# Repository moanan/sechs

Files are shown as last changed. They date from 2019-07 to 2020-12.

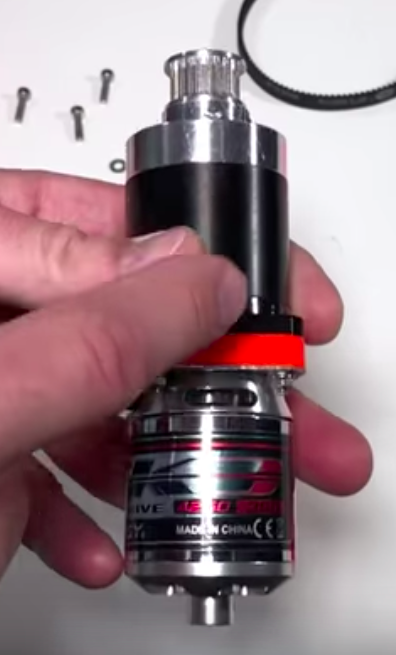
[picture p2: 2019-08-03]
2-hardware/motor/Screenshot 2019-07-31 at 23.09.07.png

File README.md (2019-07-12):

# sechs

直接在main.py中定义robot的dh参数，工具，负载，角加速度。

调用robot.frame得到各个轴的空间方位

调用robot.frame.origin得到各个轴的空间位置

调用robot.torque(tool, payload, acceleration)得到各个轴所需的转矩

调用robot.visualization(tool, payload, acceleration)可视化

torque的计算方法：

  第i个轴的torque为：abs(往后各轴以及末端负载对第i轴z_axis的力矩和) + 往后各轴以及末端负载的总惯性矩 * 预设的角加速度

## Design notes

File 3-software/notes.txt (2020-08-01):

DH parameters to urdf file: https://adohaha.github.io/DH2URDF/

```
ssh sechs@192.168.179.121
```
password: ubuntu
vncserver password: 123456

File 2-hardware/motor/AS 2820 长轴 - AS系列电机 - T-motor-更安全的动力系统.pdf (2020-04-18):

18/04/2020 | AS 2820 长轴 - AS系列电机 - T-motor-更安全的动⼒系统

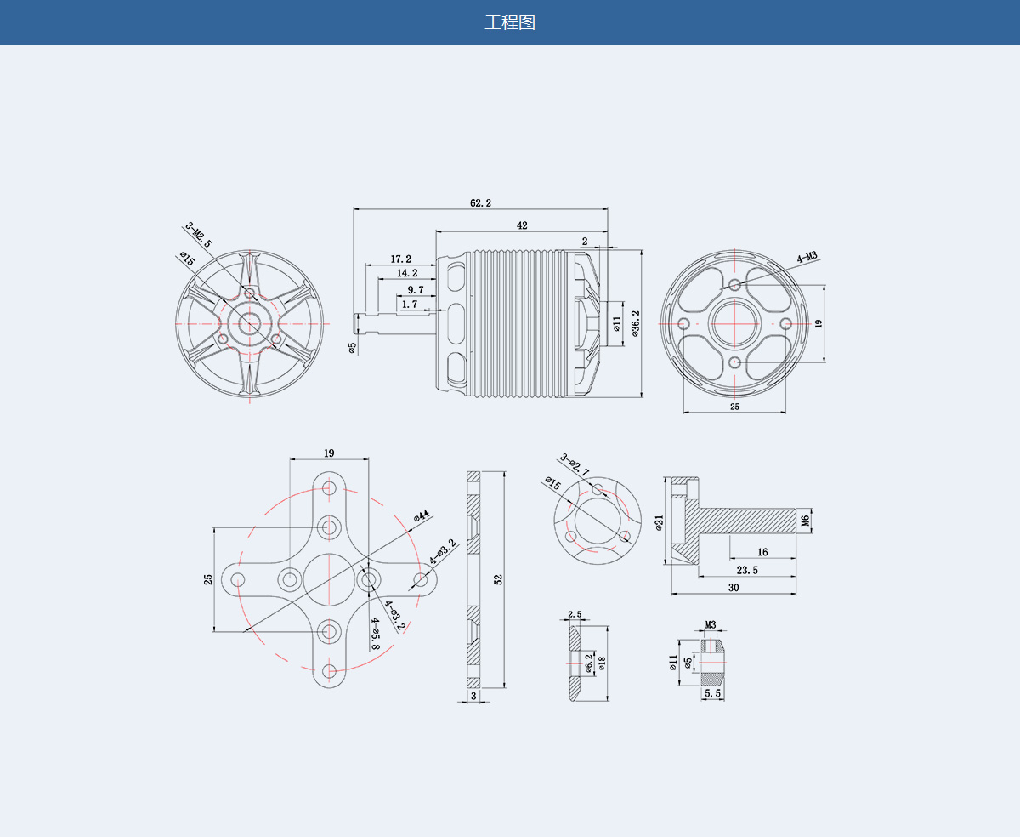
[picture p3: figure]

uav-cn.tmotor.com/html/uav/html/2019/as_1129/312.html | 1/6
AS 2820 ⻓轴 | 详情 | 参数 | ⽴即购买 (http://store-cn.tmotor.com/goods.php?id=921)

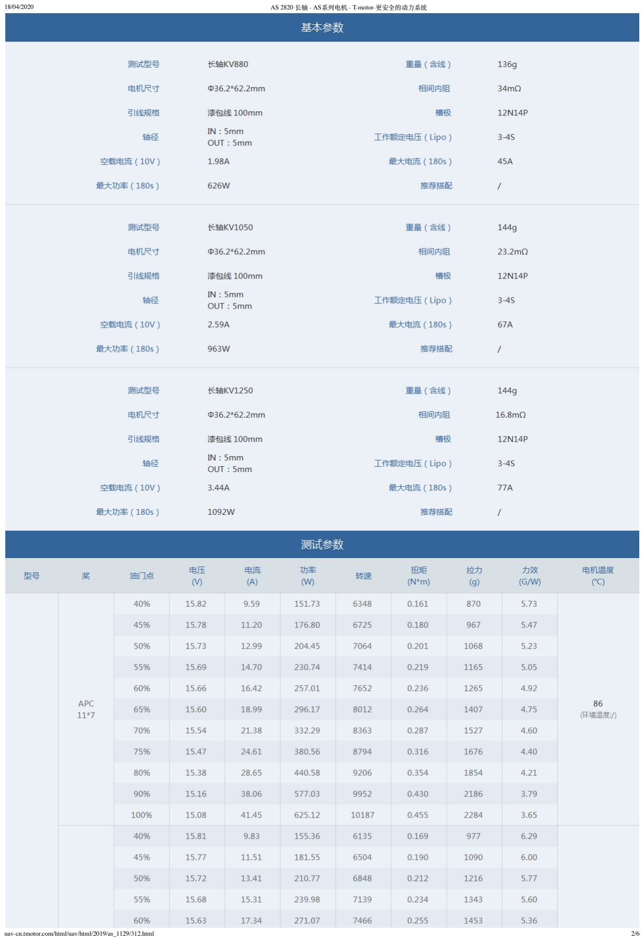
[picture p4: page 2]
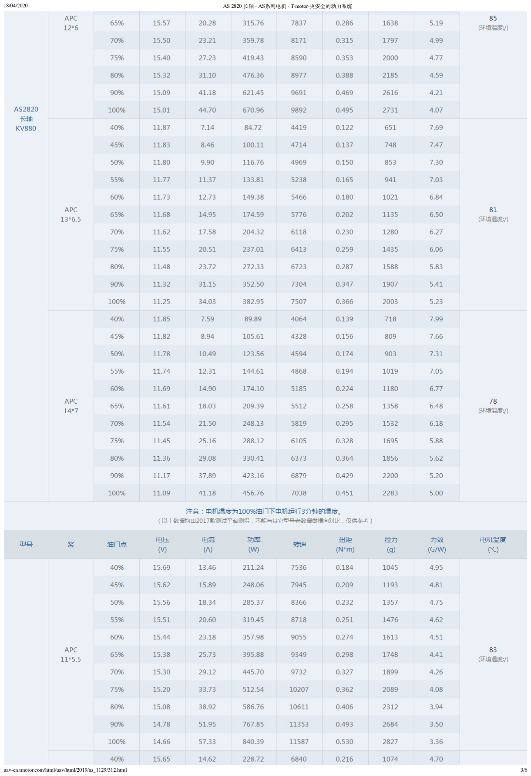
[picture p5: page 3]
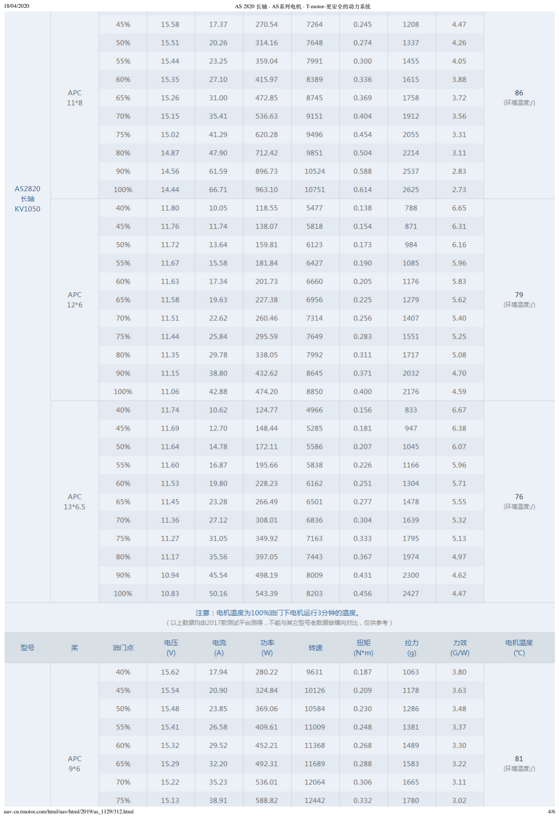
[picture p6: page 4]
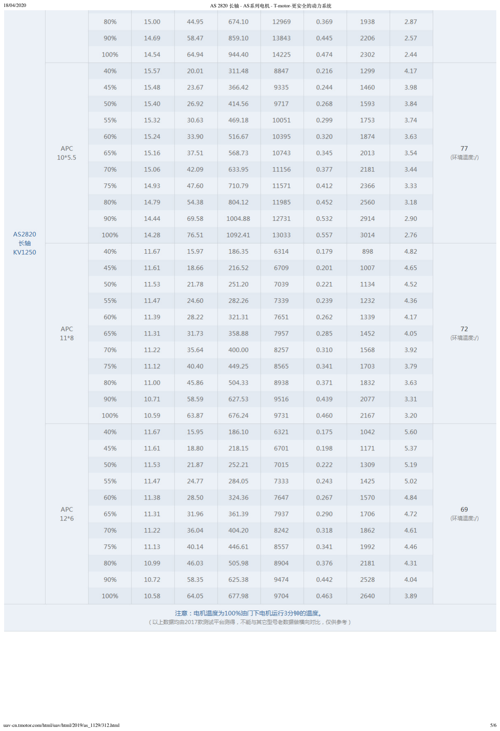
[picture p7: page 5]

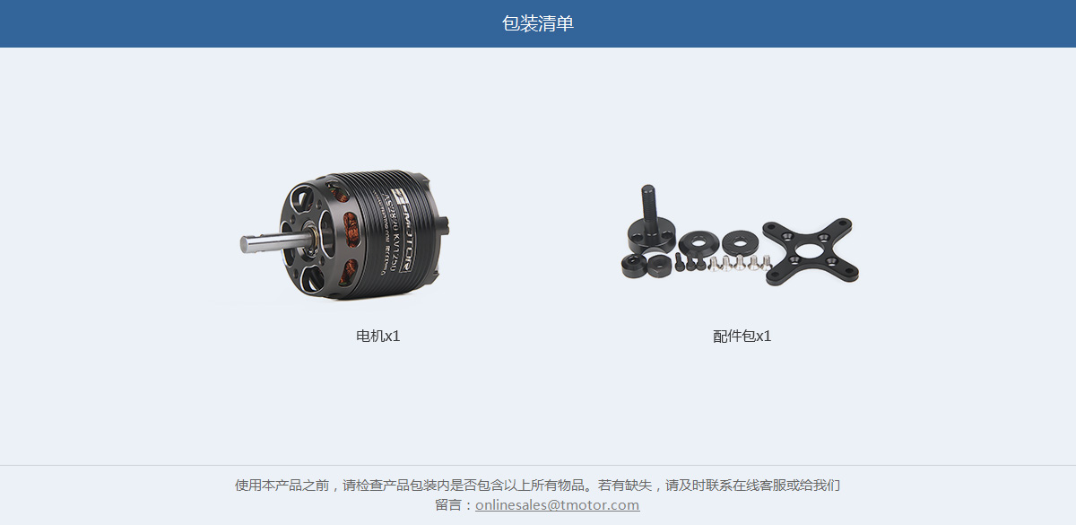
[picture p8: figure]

## English (http://uav-en.tmotor.com/)

关于我们 | | 联系我们 | | 加⼊我们 | | 精彩动态 | | 授权经销商 (https://www.facebook.com/rctigermotor)

## Copyright © 2003-2018 T-motor, All rights reserved. 赣ICP备17011325号-1

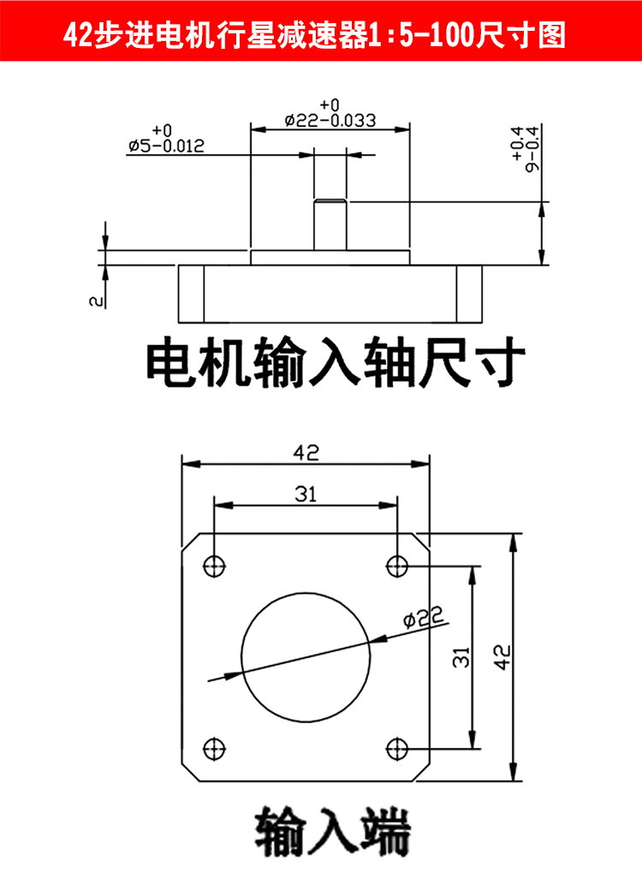
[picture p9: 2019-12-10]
2-hardware/gearbox/d1.jpg

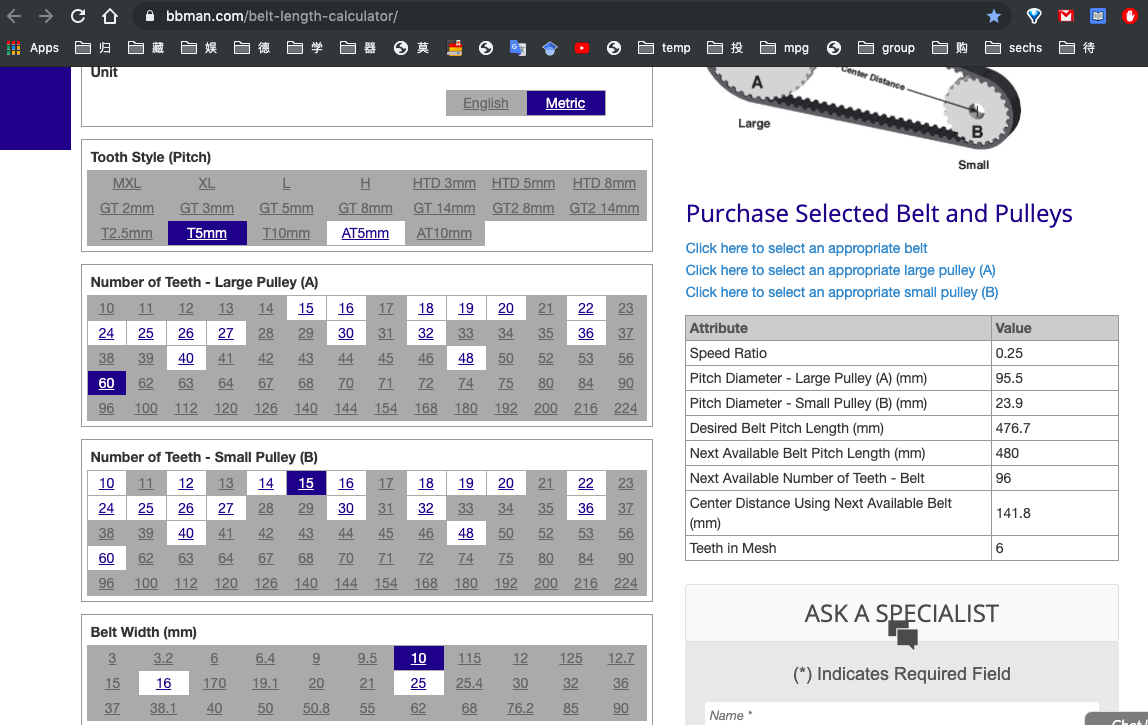
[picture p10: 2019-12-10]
2-hardware/timming belt/Screenshot 2019-11-13 at 22.11.02.png

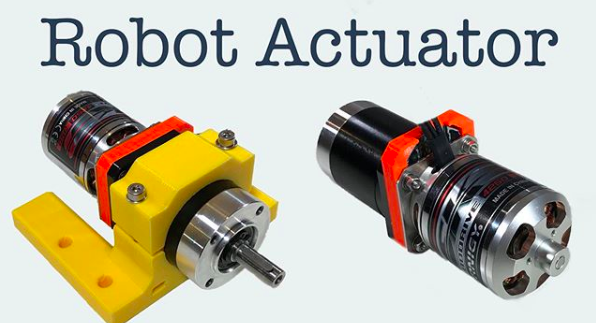
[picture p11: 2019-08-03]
2-hardware/motor/Screenshot 2019-07-31 at 22.52.01.png

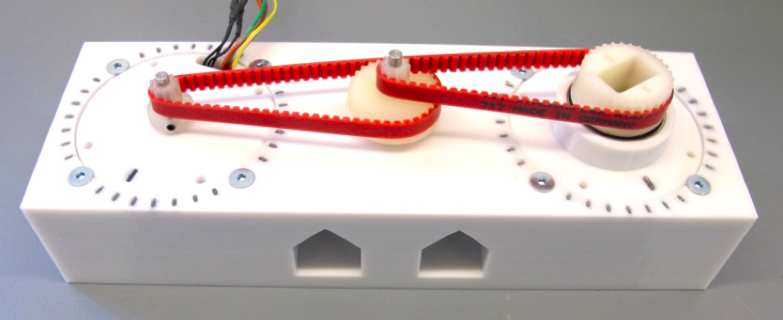
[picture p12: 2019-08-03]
2-hardware/motor/Screenshot 2019-07-21 at 15.00.27.png

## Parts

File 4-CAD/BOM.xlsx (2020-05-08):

Item | Part Number | Thumbnail | BOM Structure | Unit QTY | QTY | Stock Number | Description | REV
1 | 101-bottom | (NonDisplayable) | Normal | 1 | 1
2 | Synchronous Belt | *Varies* | Normal | 1 | 2
3 | Synchronous Pulley1 | *Varies* | Normal | 1 | 2
4 | Synchronous Pulley2 | *Varies* | Normal | 1 | 2
6 | AS5047 | (NonDisplayable) | Normal | 1 | 3
7 | magnet-6x2.5 | (NonDisplayable) | Normal | 1 | 3
8 | J1-sketch | *Varies* | Normal | 1 | 2
9 | X6215S | (NonDisplayable) | Normal | 1 | 1
10 | 104-motor-case-new | (NonDisplayable) | Normal | 1 | 1
11 | 201- | *Varies* | Normal | 1 | 3
19 | 901-4250 house | (NonDisplayable) | Normal | 1 | 2
20 | 911-42-reducer-long | (NonDisplayable) | Normal | 1 | 2
21 | Lower_Can | (NonDisplayable) | Normal | 1 | 2
22 | Shaft | (NonDisplayable) | Normal | 1 | 2
23 | Lower_Cap | (NonDisplayable) | Normal | 1 | 2
24 | Power Cables | (NonDisplayable) | Normal | 1 | 2
25 | 6mm Bearing | (NonDisplayable) | Normal | 1 | 2
26 | 5 to 6 mm bushing | (NonDisplayable) | Normal | 1 | 2
27 | Stator_Coils | (NonDisplayable) | Normal | 1 | 24
28 | Stator_Steel_Laminations | (NonDisplayable) | Normal | 1 | 2
29 | 98541A113_BLACK-FINISH STEEL EXTERNAL RETAINING RING_step | (NonDisplayable) | Normal | 1 | 2
30 | 91290A111_BLACK-OXIDE CLASS 12.9 SOCKET HEAD CAP SCREW_step | (NonDisplayable) | Normal | 1 | 8
31 | SK3 350KV Upper Assembly_MODEL | (NonDisplayable) | Normal | 1 | 2
32 | 902-4250 magnet hold | (NonDisplayable) | Normal | 1 | 2
33 | 903-4250 back | (NonDisplayable) | Normal | 1 | 2
37 | 203-link left | *Varies* | Normal | 1 | 2
42 | J4-dummy | (NonDisplayable) | Normal | 1 | 1
5 | 61814-2RS1 | (NonDisplayable) | Purchased | 1 | 2 |  | BB1_001_101-Deep groove ball bearings
18 | 61807-2RS1 | (NonDisplayable) | Purchased | 1 | 4 |  | BB1_001_101-Deep groove ball bearings
38 | W 638/3-2Z | (NonDisplayable) | Purchased | 1 | 4 |  | BB1_001_101-Deep groove ball bearings
41 | W 61705-2RZ | (NonDisplayable) | Purchased | 1 | 1 |  | BB1_001_101-Deep groove ball bearings
14 | ISO 4032 - M2 | (NonDisplayable) | Purchased | 1 | 12 |  | Hex Nut. Product grades A and B
44 | ISO 4032 - M3 | (NonDisplayable) | Purchased | 1 | 2 |  | Hex Nut. Product grades A and B
12 | ISO 10642 - M3 x 20 | (NonDisplayable) | Purchased | 1 | 4 |  | Hexagon Socket Countersunk Head Screw
15 | ISO 10642 - M4 x 16 | (NonDisplayable) | Purchased | 1 | 3 |  | Hexagon Socket Countersunk Head Screw
39 | ISO 10642 - M4 x 20 | (NonDisplayable) | Purchased | 1 | 8 |  | Hexagon Socket Countersunk Head Screw
13 | ISO 4762 - M2 x 6 | (NonDisplayable) | Purchased | 1 | 12 |  | Hexagon Socket Head Cap Screw
16 | ISO 4762 - M3 x 10 | (NonDisplayable) | Purchased | 1 | 13 |  | Hexagon Socket Head Cap Screw
17 | ISO 4762 - M4 x 20 | (NonDisplayable) | Purchased | 1 | 6 |  | Hexagon Socket Head Cap Screw
35 | ISO 4762 - M3 x 16 | (NonDisplayable) | Purchased | 1 | 8 |  | Hexagon Socket Head Cap Screw
36 | ISO 4762 - M2.5 x 12 | (NonDisplayable) | Purchased | 1 | 6 |  | Hexagon Socket Head Cap Screw
40 | ISO 4762 - M3 x 12 | (NonDisplayable) | Purchased | 1 | 12 |  | Hexagon Socket Head Cap Screw
43 | ISO 4762 - M3 x 20 | (NonDisplayable) | Purchased | 1 | 2 |  | Hexagon Socket Head Cap Screw
45 | ISO 4762 - M3 x 25 | (NonDisplayable) | Purchased | 1 | 14 |  | Hexagon Socket Head Cap Screw
34 | DIN 7991 - M3x12 | (NonDisplayable) | Purchased | 1 | 8 |  | Hexagon socket countersunk head cap screws

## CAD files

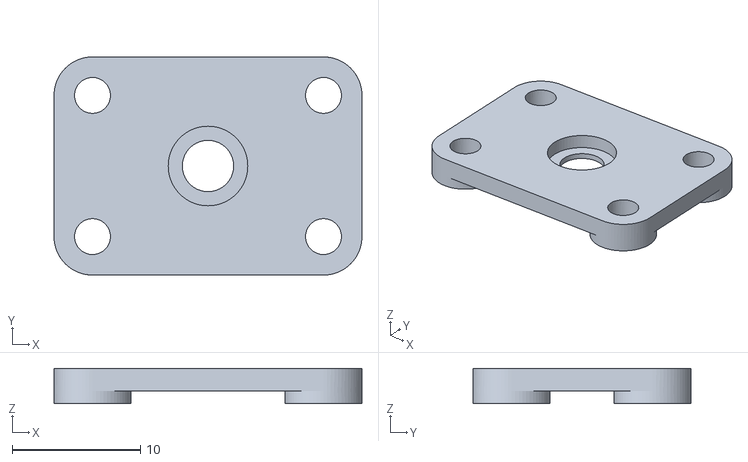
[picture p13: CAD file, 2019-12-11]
2-hardware/encoder/test_encoder.stl
24.0 x 17.0 x 2.75

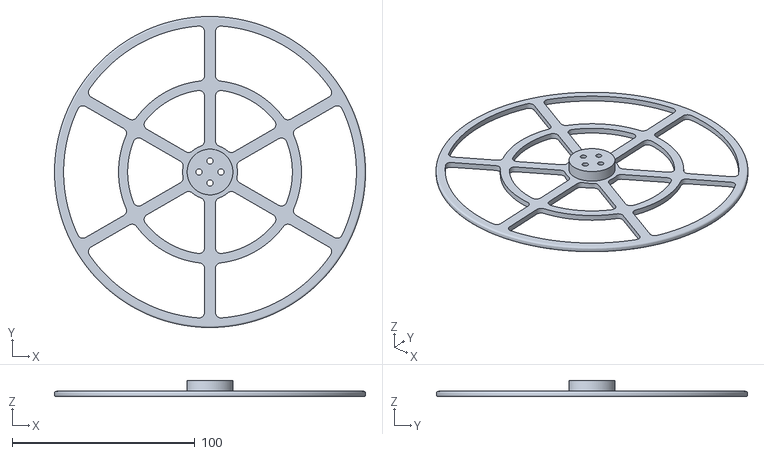
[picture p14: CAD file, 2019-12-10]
4-CAD/tester/fly.stl
170.0 x 170.0 x 9.00

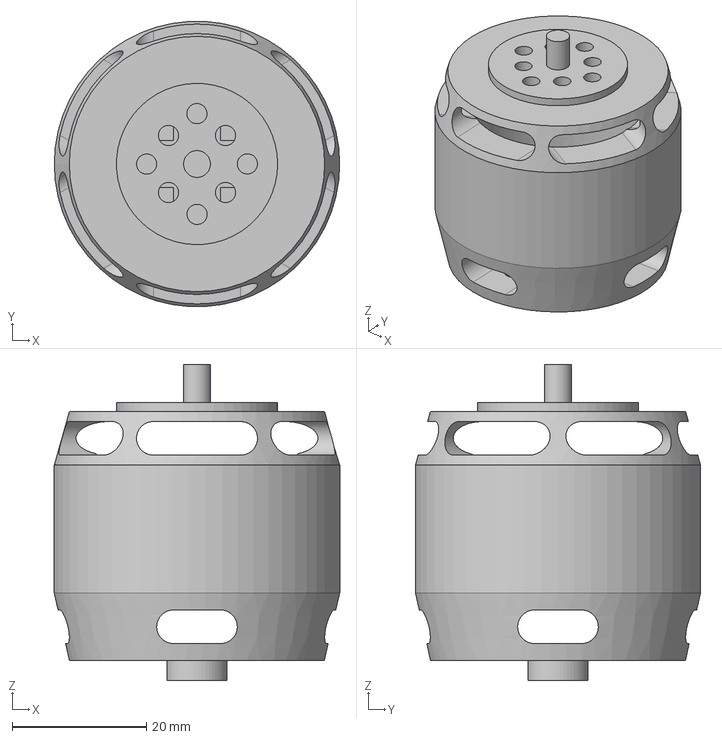
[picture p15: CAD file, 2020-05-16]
4-CAD/standardParts/AS 2820 kv880/T-MOTOR_U5 .step
42.5 x 42.4 x 47.0 mm

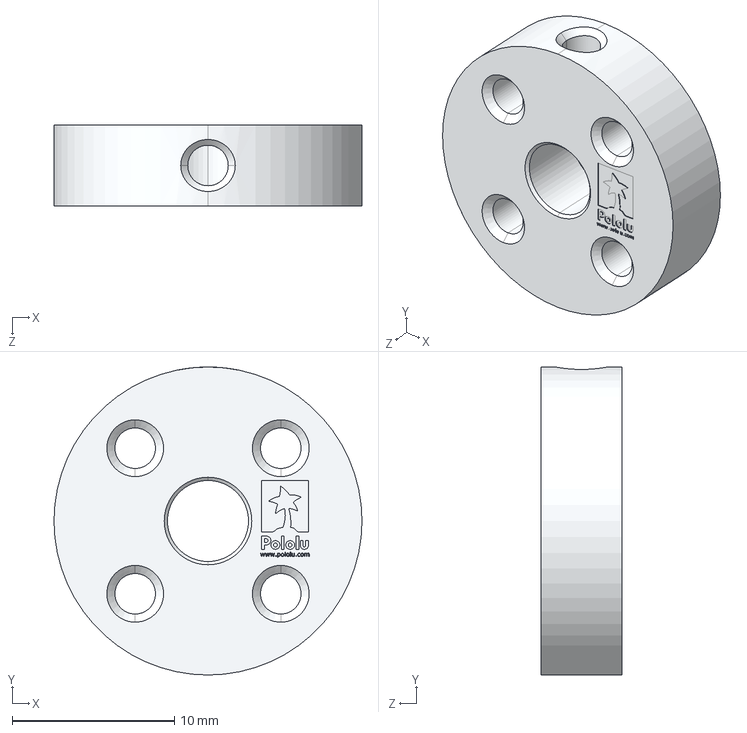
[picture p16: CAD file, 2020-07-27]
4-CAD/standardParts/Pololu mounting hub/pololu-universal-aluminum-mounting-hub-for-5mm-shaft-m3-holes.step
19.0 x 19.0 x 5.00 mm

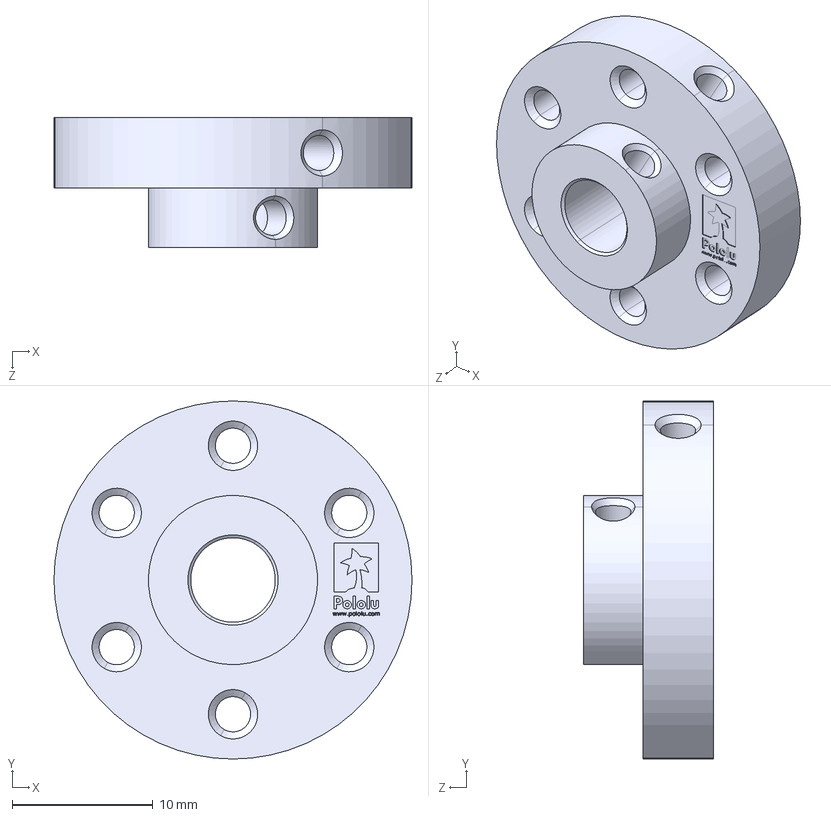
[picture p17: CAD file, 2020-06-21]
4-CAD/standardParts/Pololu mounting hub/pololu-universal-aluminum-mounting-hub-for-6mm-shaft-m3-holes.step
25.4 x 25.4 x 9.20 mm

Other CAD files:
4-CAD/standardParts/Pololu mounting hub/pololu-universal-aluminum-mounting-hub-for-8mm-shaft-m3-holes.step
2-hardware/encoder/test_encoder.3dm
4-CAD/10-J1.iam
4-CAD/10-J1_new.iam
4-CAD/102-top-motor-adapt-big-motor.ipt
4-CAD/102-top-motor.ipt
4-CAD/103-top-output.ipt
4-CAD/104-motor-case-new.ipt
4-CAD/104-motor-case.ipt
4-CAD/105-flange adapter.ipt
4-CAD/106-pulley adapter.ipt
4-CAD/111-base template.ipt
4-CAD/112-base middle.ipt
4-CAD/113-base bottom.ipt
4-CAD/114-base top.ipt
4-CAD/20-J2.iam
4-CAD/200-link template.ipt
4-CAD/201-flange-with motor.ipt
4-CAD/203-dummy.iam
4-CAD/203-link left-dummy dowm.ipt
4-CAD/203-link left-dummy up.ipt
4-CAD/203-link left.ipt
4-CAD/30-J3.iam
4-CAD/303-dummy.iam
4-CAD/303-link right-dummy down.ipt
4-CAD/303-link right-dummy up.ipt
4-CAD/303-link right.ipt
4-CAD/40-J4.iam
4-CAD/401-flange.ipt
4-CAD/402-gearbox-housing-cap.ipt
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

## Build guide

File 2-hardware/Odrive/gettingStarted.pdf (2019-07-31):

- Connect the three phases of one or both motors
- connect the brake resistor to AUX + and AUX - (resistor has no polarity)
- connect the ABI encoder (5 pins: A, B, I (or X, Z), 5V and GND)
- connect the oDrive to the computer via USB
- check that the switch on SW1 is on RUN, not on DFU (= device firmware update)
- connect the oDrive DC+ and DC- to a direct current power supply (pay attention to polarity); minimum voltage for all board versions is 12 VDC
- download and install odrivetool following these
steps: https://docs.odriverobotics.com/#downloading-and-installing-tools (offline version Getting Started _ ODrive.pdf)
- in your bash/shell, move to the directory that has odrivetool, typically in odrive/tools/, and run the tool by typing ./odrivetool; for Windows, see description on oDrive homepage(Link)
- turn on power supply with at least half of the oDrive's maximum voltage (there are 24V oDrives and 48V oDrives, higher voltages may be available online soon are available in the oDrive shop), start with low maximal current, e. g. 2A
- check if the PWR LED on your oDrive is on
- odrivetool should recognize the oDrive after some seconds
but if you want a specific oDrive to be connected, type $ ./odrivetool --serial-number <your serial number here>
set up for the motor (in this example, connected to M0, which odrivetool knows
as axis0)
- odrivetool should automatically recognize the odrive and put out a 'connected' notice
- to inspect all available parameters and variables, type odrv0 (or odrv1, depending on how many oDrives are connected)
- you can go into deeper variable levels pertaining to python objects by typing for example odrv0.config or odrv0.axis0
- first, make sure the motor will not get overloaded, so set limits (the values given here are for a T-Motor MN4006-23, 0.3A idle current, 16 A max current)
- odrv0.axis0.motor.config.current_lim = 2
- odrv0.axis0.controller.config.vel_limit = 2000 (velocity is in encoder counts / sec)
- odrv0.axis0.motor.config.calibration_current = 1
- odrv0.config.brake_resistance = 2.0
- odrv0.axis0.motor.config.pole_pairs = 12

•

# Getting started - oDrive V3.5

Wednesday, 31. July 2019 09:05

- odrv0.axis0.motor.config.pole_pairs = 12
- odrv0.axis0.motor.config.motor_type = 0 (for high current motors; for gimbal motors set motor_type = 1)
- odrv0.axis0.encoder.config.cpr = 8192 (CPR = 4xPPR, PPR being the pulses per rotation for one channel. You have to multiply by 4, since oDrive is counting both rising and falling edges for both A and B channel)
- odrv0.save_configuration() (keep this command in mind since for many errors, this command followed by odrv0.reboot() helps)
- odrv0.reboot()
now do the calibration, save and reboot again:
odrv0.axis0.requested_state = AXIS_STATE_FULL_CALIBRATION_SEQUENCE

○

•

for now, control should work; type
- odrv0.axis0.requested_state = AXIS_STATE_CLOSED_LOOP_CONTROL ← this automatically sets position control
- if calibration fails in the first place and the coils are not powered,
set odrv0.axis0.controller.config.vel_limit_tolerance = 0.0
- please not that this setting makes the controller IGNORE any velocity overshoot!

•

- tune the controller via its parameters, which you can all check by typing
- odrv0.axis0.controller.config
- you can change control mode in odrvX.axisX.controller.config.control_mode (for control modes see below)
- if you use the same motor each time, you can avoid the calibration required at each startup by typing odrv0.axis0.motor

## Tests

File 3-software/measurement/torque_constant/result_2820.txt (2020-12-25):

# =============================
# axis_3: T-Motor AS-2820 KV880
# =============================

result:
	k = 0.01095249
	b = 0.00203316

current force

0.4A 12g

0.8A 14g

1.2A 16g

1.6A 18g

2.0A 21g

2.4A 22.5g

2.8A 25g

3.2A 27g

3.6A 28g

4.0A 31g

4.4A 33g

4.8A 36g

5.2A 37g

5.6A 39g

6.0A 42g

6.4A 45g

6.8A 47g

7.2A 49g

7.6A 51g

8.0A 54g

8.4A 56g

8.8A 58g

9.2A 61g

9.6A 63g

10.0A 65g

10.4A 67.5g

10.8A 69.5g

11.2A 72g

11.6A 74g

12.0A 76g

12.4A 78g

12.8A 80g

13.2A 83g

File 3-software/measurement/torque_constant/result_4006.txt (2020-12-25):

# ===============================
# axis_0: T-Motor MN4006-23 KV380
# ===============================

result:
	k = 0.02237971
	b = -0.00778521

current force

0.4A 7g

0.8A 12g

1.2A 16g

1.6A 21g

2.0A 27g

2.4A 31g

2.8A 36g

3.2A 41g

3.6A 45.5g

4.0A 50g

4.4A 55g

4.8A 59.5g

5.2A 64g

5.6A 69g

6.0A 73g

6.4A 78g

6.8A 82g

7.2A 87g

7.6A 92g

8.0A 96g

8.4A 100g

8.8A 105g

9.2A 108g

9.6A 114g

10.0A 119g

10.4A 123g

10.8A 128g

11.2A 132g

11.6A 136g

12.0A 139g

12.4A 144g

12.8A 149g

13.2A 153g

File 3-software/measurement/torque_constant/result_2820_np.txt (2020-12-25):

0.4 12
0.8 14
1.2 16
1.6 18
2.0 21
2.4 22.5
2.8 25
3.2 27
3.6 28
4.0 31
4.4 33
4.8 36
5.2 37
5.6 39
6.0 42
6.4 45
6.8 47
7.2 49
7.6 51
8.0 54
8.4 56
8.8 58
9.2 61
9.6 63
10.0 65
10.4 67.5
10.8 69.5
11.2 72
11.6 74
12.0 76
12.4 78
12.8 80
13.2 83

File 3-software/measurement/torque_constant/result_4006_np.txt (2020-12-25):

0.4 7
0.8 12
1.2 16
1.6 21
2.0 27
2.4 31
2.8 36
3.2 41
3.6 45.5
4.0 50
4.4 55
4.8 59.5
5.2 64
5.6 69
6.0 73
6.4 78
6.8 82
7.2 87
7.6 92
8.0 96
8.4 100
8.8 105
9.2 108
9.6 114
10.0 119
10.4 123
10.8 128
11.2 132
11.6 136
12.0 139
12.4 144
12.8 149
13.2 153

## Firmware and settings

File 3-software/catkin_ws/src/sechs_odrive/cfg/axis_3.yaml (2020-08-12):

# =============================
# axis_3: T-Motor AS-2820 KV880
# =============================

axis_3:

  # ----------------
  # basic properties
  # ----------------

  reduction: 19.2
  direction: -1 # 0: +(counter-clockwise) 1: -(clockwise) 
  init_offset: -368.0

  # --------
  # start-up
  # --------

  startup_encoder_index_search: True

  # -------------
  # motor related
  # -------------

  motor_config:
    pre_calibrated: True
    pole_pairs: 7
    # current limit
    current_lim: 25.0 # (A)
    calibration_current: 10.0 # (A)
    current_lim_tolerance: 1.25

  # ---------------
  # encoder related
  # ---------------

  encoder_config:
    pre_calibrated: True
    cpr: 4000
    use_index: True

  # ----------
  # controller
  # ----------

  controller_config:
    vel_limit: 9261.0 # (encoder counts / sec)
    vel_limit_tolerance: 2.6
    pos_gain: 100.0
    vel_gain: 0.0006
    vel_integrator_gain: 0.0
    control_mode: 3 # position control (default)

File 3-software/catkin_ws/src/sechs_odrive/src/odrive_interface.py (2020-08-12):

#!/usr/bin/env python3

from __future__ import print_function

import odrive
import time
from odrive.enums import *
from math import pi

import rospy
from sechs_odrive.msg import *
# from sensor_msgs.msg import Joy


class Sechs:
    def __init__(self):

        # --------------------------
        # find odrives and load axes
        # --------------------------
        
        odrv0 = odrive.find_any(serial_number="208A3592524B") # 56V axis_1 axis_2
        rospy.loginfo("odrive_0 found!")
        odrv1 = odrive.find_any(serial_number="2083359F524B") # 24V_taobao axis_3 axis_4
        rospy.loginfo("odrive_1 found!")
        odrv2 = odrive.find_any(serial_number="385D37803437") # 24V axis_0 
        rospy.loginfo("odrive_2 found!")
        self.axes = []
        self.axes.append(odrv2.axis0)
        self.axes.append(odrv0.axis0)
        self.axes.append(odrv0.axis1)
        self.axes.append(odrv1.axis0)
        self.axes.append(odrv1.axis1)

        # -------------------------------------------
        # load directions, reductions, initial offset
        # -------------------------------------------

        self.directions = []
        self.reductions = []
        self.init_offset = []
        for i in range(6):
            self.directions.append(rospy.get_param(("/axis_%d/direction" % i), default=0))
            self.reductions.append(rospy.get_param(("/axis_%d/reduction" % i), default=1.0))
            self.init_offset.append(rospy.get_param(("/axis_%d/init_offset" % i), default=0.0))
        
        # -------------------------------
        # load control related parameters
        # -------------------------------

        for i in range(0, 5):
            # self.axes[i].config.startup_encoder_index_search = rospy.get_param(("/axis_%d/startup_encoder_index_search" % i))
            # self.axes[i].motor.config.pre_calibrated = rospy.get_param(("/axis_%d/motor_config/pre_calibrated" % i))
            # self.axes[i].motor.config.pole_pairs = rospy.get_param(("/axis_%d/motor_config/pole_pairs" % i))
            self.axes[i].motor.config.current_lim = rospy.get_param(("/axis_%d/motor_config/current_lim" % i))
            self.axes[i].motor.config.calibration_current = rospy.get_param(("/axis_%d/motor_config/calibration_current" % i))
            self.axes[i].motor.config.current_lim_tolerance = rospy.get_param(("/axis_%d/motor_config/current_lim_tolerance" % i))
            # self.axes[i].encoder.config.pre_calibrated = rospy.get_param(("/axis_%d/encoder_config/pre_calibrated" % i))
            # self.axes[i].encoder.config.cpr = rospy.get_param(("/axis_%d/encoder_config/cpr" % i))
            # self.axes[i].encoder.config.use_index = rospy.get_param(("/axis_%d/encoder_config/use_index" % i))
            self.axes[i].controller.config.vel_limit = rospy.get_param(("/axis_%d/controller_config/vel_limit" % i))
            self.axes[i].controller.config.vel_limit_tolerance = rospy.get_param(("/axis_%d/controller_config/vel_limit_tolerance" % i))
            self.axes[i].controller.config.pos_gain = rospy.get_param(("/axis_%d/controller_config/pos_gain" % i))
            self.axes[i].controller.config.vel_gain = rospy.get_param(("/axis_%d/controller_config/vel_gain" % i))
            self.axes[i].controller.config.vel_integrator_gain = rospy.get_param(("/axis_%d/controller_config/vel_integrator_gain" % i))
            # self.axes[i].controller.config.control_mode = rospy.get_param(("/axis_%d/controller_config/control_mode" % i))
            pass
    
    def start_closed_loop(self):
        # rospy.loginfo("start calibration")
        # for i in range(0, 5):
        #     rospy.loginfo("calibrating axis_%d" % i)
        #     self.axes[i].requested_state = AXIS_STATE_ENCODER_INDEX_SEARCH
        #     time.sleep(1)
        for i in range(0, 5):
            rospy.loginfo("axis_%d entering closed loop control!" % i)
            self.axes[i].requested_state = AXIS_STATE_CLOSED_LOOP_CONTROL
            time.sleep(1)
        self.home()
    
    def home(self):
        self.move_axes([0.0]*6)

    def close(self):
        self.move_to([-500.0, -500.0, -500.0, -500.0, -500.0, 0.0]) # end pose
        time.sleep(1)
        for i in range(0, 5):
            rospy.loginfo("axis_%d closed!" % i)
            self.axes[i].requested_state = AXIS_STATE_IDLE
            time.sleep(1)

    @property
    def axes_feedback(self):
        sensor_msg = Sechs_State()
        # pos
        for i in range(0, 5):
            sensor_msg.pos.values[i] = (self.axes[i].encoder.pos_estimate + self.init_offset[i]) * pi * self.directions[i] / 2000.0 / self.reductions[i]
        sensor_msg.pos.values[2] -= sensor_msg.pos.values[1]  # joint 2 velocity coupled
        # cur
        for i in range(0, 5):
            sensor_msg.cur.values[i] = self.axes[i].motor.current_control.Iq_measured
        return sensor_msg
    
    def move_to(self, values):
        # count in cpr
        for i in range(0, 5):
            # sechs.axes[i].controller.move_to_pos(values[i])
            sechs.axes[i].controller.pos_setpoint = values[i]

    def move_axes(self, values):
        values_cpr = [0.0] * 6
        for i in range(0, 6):
            if i == 2:  # joint 2 velocity coupled
                values_cpr[i] = (values[i] + values[1]) * 2000.0 * sechs.reductions[i] * self.directions[i] / pi - self.init_offset[i]
            else:
                values_cpr[i] = values[i] * 2000.0 * sechs.reductions[i] * self.directions[i] / pi - self.init_offset[i]
        self.move_to(values_cpr)


def callback_pos_command(pos_command):
    global sechs
    # rospy.loginfo("pos_1: %f", pos_command.values[1])
    sechs.move_axes(pos_command.values)


rospy.init_node('odrive_interface', anonymous=False)
rospy.loginfo("odrive_interface init...")
sechs = Sechs()
sechs.start_closed_loop()

# rospy.loginfo("%f", sechs.axes[1].controller.config.vel_gain)
rospy.Subscriber('Sechs/Position_Command', Sechs_Pos, callback_pos_command)
pub = rospy.Publisher('Sechs/Encoder_Feedback', Sechs_State , queue_size=10)

rate = rospy.Rate(100) 
while not rospy.is_shutdown():
    pub.publish(sechs.axes_feedback)
    rate.sleep()

sechs.close()
# rospy.spin()

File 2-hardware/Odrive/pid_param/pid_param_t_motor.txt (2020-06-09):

2019_12_07 T_MOTORMN4006-23 KV380
CPR: 8192 POLE_PAIRS: 12 

odrv0.axis0.controller.config 
	vel_limit = 200000.0 (float)
	pos_gain = 103.0 (float)
	vel_integrator_gain = 0.00 (float)
	vel_ramp_rate = 10000.0 (float)
	control_mode = 3 (int)
	vel_limit_tolerance = 1.2000000476837158 (float)
	vel_gain = 0.0001 (float)
	setpoints_in_cpr = False (bool)

odrv0.axis0.config
	step_gpio_pin = 1 (int)
	calibration_lockin:
	  ramp_time = 0.4000000059604645 (float)
	  vel = 40.0 (float)
	  current = 10.0 (float)
	  ramp_distance = 3.1415927410125732 (float)
	  accel = 20.0 (float)
	startup_closed_loop_control = False (bool)
	enable_step_dir = False (bool)
	startup_encoder_index_search = False (bool)
	sensorless_ramp:
	  finish_on_vel = True (bool)
	  accel = 200.0 (float)
	  vel = 400.0 (float)
	  current = 10.0 (float)
	  finish_distance = 100.0 (float)
	  ramp_time = 0.4000000059604645 (float)
	  finish_on_distance = False (bool)
	  finish_on_enc_idx = False (bool)
	  ramp_distance = 3.1415927410125732 (float)
	startup_motor_calibration = False (bool)
	watchdog_timeout = 0.0 (float)
	startup_sensorless_control = False (bool)
	startup_encoder_offset_calibration = False (bool)
	counts_per_step = 2.0 (float)
	general_lockin:
	  finish_on_vel = False (bool)
	  accel = 20.0 (float)
	  vel = 40.0 (float)
	  current = 10.0 (float)
	  finish_distance = 100.0 (float)
	  ramp_time = 0.4000000059604645 (float)
	  finish_on_distance = False (bool)
	  finish_on_enc_idx = False (bool)
	  ramp_distance = 3.1415927410125732 (float)
	dir_gpio_pin = 2 (int)

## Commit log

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2019-11-07 start design
    [101-bottom.ipt, 61807-2RS1.iam, 61807-2RS1_PART1.ipt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]
2019-11-13 belt design for J1
    [101-bottom.0003.ipt, 101-bottom.ipt, 61814-2RS1.0001.iam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]
2019-11-18 add sk3 4250 BLDC motor
    [5 to 6 mm bushing.ipt, 6mm Bearing.ipt, 91290A111_BLACK-OXIDE CLASS 12.9 SOCKET HEAD CAP SCREW_step.ipt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]
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2019-11-24 align encoder; to do: connection to top
    [101-bottom.0008.ipt, 101-bottom.0020.ipt, 101-bottom.ipt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]
2019-11-26 J1 top
    [101-bottom.0020.ipt, 101-bottom.0025.ipt, 101-bottom.ipt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]
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2019-12-10 motor gearbox connection design
    [901-4250 house.0013.ipt, 901-4250 house.ipt, 902-4250 magnet hold.0004.ipt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]
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2019-12-11 some encoder test setup added
    [test_encoder.3dm, test_encoder.stl]
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2020-01-02 fix dimension
    [901-4250 house.0015.ipt, 901-4250 house.0019.ipt, 901-4250 house.ipt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]
2020-01-04 update back housing of motor module
    [903-4250 back.0020.ipt, 903-4250 back.0025.ipt, 903-4250 back.ipt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]
2020-01-04 fix dimension again
    [903-4250 back.0025.ipt, 903-4250 back.0028.ipt, 903-4250 back.ipt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]
2020-01-05 new pid params added
    [pid_param_t_motor.txt, pid_param_turnigy.txt]
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2020-02-15 add J1 motor CAD
    [X6215S.0011.ipt, X6215S.ipt]
2020-02-15 update J1 motor case
    [104-motor-case.0047.ipt, 104-motor-case.ipt, Synchronous Pulley11.0005.ipt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]
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2020-03-19 add dummy belt for J3
    [20-J2.0013.iam, 20-J2.0017.iam, 20-J2.iam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]
2020-03-20 update J3 motor position
    [20-J2.0017.iam, 20-J2.0023.iam, 20-J2.iam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]
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2020-05-08 export stl. export BOM
    [201-flange-with motor.0043.ipt, 201-flange-with motor.0044.ipt, 201-flange-with motor.ipt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]
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2020-05-16 add J2 J3 link dummy print
    [105-flange adapter.0046.ipt, 105-flange adapter.0048.ipt, 105-flange adapter.ipt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]
2020-05-16 update bearing fit dimension; 3D printing of dummy stl needs to save assembly to simplfied part first, then export to stl in 3D printing environment (take care of unit)
    [203-dummy.0001.iam, 203-dummy.0001_1.iam, 203-dummy.0003.iam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]
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2020-06-03 untrack OldVersions in CAD files
    [10-J1.0055.iam, 101-bottom.0031.ipt, 102-top-motor-adapt-big-motor.0025.ipt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]
2020-06-03 extend J2J3 flange adapter
    [105-flange adapter.ipt]
2020-06-03 add rim on J1 small pulley
    [10-J1.iam, 105-flange adapter.stl, 20-J2.iam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]
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2020-06-06 working of second motor module
    [912-35-reducer.ipt, 921-2820 house.ipt, 922-2820 magnet hold.ipt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]
2020-06-06 switch back to encoder AS5047
    [921-2820 house.ipt, 922-2820 magnet hold.ipt, 923-2820 back.ipt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]
2020-06-07 add screws for J4 motor unit
    [40-J4.iam, 921-2820 house.ipt, motor unit 2820.iam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]
2020-06-09 added 2 pkgs: sechs_odrive, gui
    [pid_param_sunnysky_x6215s.txt, pid_param_t_motor.txt, pid_param_turnigy.txt]
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2020-06-14 update 2820 housing dimensions
    [921-2820 house.ipt]
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2020-06-27 replace J4 bearing
    [402-gearbox-housing.ipt, W 606-2Z.iam, W 606-2Z_PART1.ipt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]
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2020-07-06 add screws for J4 J5
    [40-J4.iam, 50-J5.iam]
2020-07-06 clean screws for J1 J2
    [20-J2.iam, 30-J3.iam, 40-J4.iam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]
2020-07-15 update J2 and J3: enlarge structure and add motor hub
    [20-J2.iam, 203-link left.ipt, 30-J3.iam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]
2020-07-16 add motor hub for J3, add cable path
    [20-J2.iam, 201-flange-with motor.ipt, 203-link left.ipt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]
2020-07-27 start to design new J1 in 2-stage belt transmission
    [10-J1_new.iam, J1_belts_lower.iam, J1_belts_upper.iam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]
2020-08-05 shorter J5
    [50-J5.iam, 502-gearbox-housing.ipt, 504-shaft.ipt]
2020-08-08 finish shorter J5 design
    [50-J5.iam, 501-flange.ipt, 502-gearbox-housing-cap.ipt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]
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2020-08-23 add J6 (identical as J5 for now)
    [60-J6.iam, 601-flange.ipt, 602-gearbox-housing-cap.ipt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]
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2020-08-29 immerse J1 gearbox into pulley
    [10-J1.iam, 105-flange adapter.ipt, J1_belt.iam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]
2020-09-02 flip J1 motor
    [10-J1.iam]
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2020-09-05 add J1 motor unit
    [921-2820 house (J1).ipt, motor unit 2820 (J1).iam, motor unit 2820.iam]
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2020-09-20 re-model J1 for allowing template
    [10-J1.iam, 101-bottom.ipt, 111-base template.ipt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]
2020-10-31 J1 adapter counterbore -> countersunk
    [105-flange adapter.ipt]
2020-10-31 update base template dimension to match belt length
    [111-base template.ipt]
2020-10-31 add two more holes for bolts in base
    [111-base template.ipt, 112-base middle.ipt, 113-base bottom.ipt]
2020-10-31 redesign base-top to a whole piece
    [114-base top.ipt]
2020-10-31 fix bug: not aligned base
    [111-base template.ipt, 112-base middle.ipt, 113-base bottom.ipt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]
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2020-10-31 better J1 bolt connection
    [113-base bottom.ipt, 114-base top.ipt]
2020-10-31 mount holes for Odrives
    [10-J1.iam, 112-base middle.ipt, 113-base bottom.ipt]
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2020-11-01 replace J6 with real J5
    [10-J1.iam, 30-J3.iam, 40-J4.iam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]
2020-11-01 remove not needed files
    [504-shaft.ipt, 601-flange.ipt, 602-gearbox-housing-cap.ipt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]
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2020-11-04 enlarge bearing interface 47mm -> 47.1mm
    [203-link left.ipt, 303-link right.ipt, Synchronous Pulley11.ipt]
2020-11-08 add J2,3 link template
    [200-link template.ipt]
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2020-11-08 J2 add fixing holes for cables
    [10-J1.iam, 20-J2.iam, 201-flange-with motor.ipt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]
2020-11-29 ordered similar wrong motor: AS2820->AT2820, add modified actuator design
    [501-flange for AT2820.ipt, 931-AT2820 house.ipt, 932-AT2820 magnet hold.ipt]
2020-11-30 add measurements and pid files
    [param5.1_2820.txt, param5.1_4006.txt]
2020-12-25 shrink J2,3 width: 80mm -> 70mm
    [200-link template.ipt, 203-link left.ipt]
2020-12-25 add J2 extrusion for cables
    [203-link left.ipt]
2020-12-25 enlarge J3 pulley center hole
    [J3_belt.iam, Synchronous Belts Transmission1.iam, Synchronous Pulley21.ipt]
2020-12-25 add 4 more screws for J23
    [200-link template.ipt, 203-link left.ipt, 30-J3.iam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]
2020-12-25 add cable output fixure
    [203-link left.ipt]
2020-12-25 add driving dimension in spread sheet
    [20-J2.iam, 200-link template.ipt, 201-flange-with motor.ipt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]
2020-12-26 add more driving dimensions
    [10-J1.iam, 105-flange adapter.ipt, 112-base middle.ipt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]
2021-01-23 enlarge J3 small pulley center hole
    [200-link template.ipt, 201-flange-with motor.ipt, 30-J3.iam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]
